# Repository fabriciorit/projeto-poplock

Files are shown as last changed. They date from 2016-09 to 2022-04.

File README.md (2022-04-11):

# Trava eletrônica controlada por padrão sonoro
Responsáveis: Caio Vinícius Batista Pereira e Fabrício Ribeiro Toloczko

## Introdução e Justificativa
A automatização residencial tem se tornado cada vez mais comum e mais barata. E uma das facilidades trazidas por este tipo de aplicação tecnológica é a dependência cada vez menor de falhas humanas. É comum as pessoas perderem ou esquecerem as chaves para entrar em casa, e muitas vezes as pessoas tem dificuldades para lembrar senhas. Músicas são trechos sonoros facilmente memorizáveis, além disso extremamente seguros, pois o número de músicas existentes é muito grande e disperso. 

## Especificação do Produto
* Reconhecimento de pelo menos 5 segundos de padrão sonoro;
* Resposta em frequência garantida para frequências médias(200Hz a 1500Hz);
* Tensão de alimentação 110/220V;
* Bateria de emergência;
* Gravação por microfone(eletreto);
* Acionamento de uma trava elétrica 12V de até 1A;
* Comunicação via módulo Wi-Fi usando TCP/IP;
* Interface com usuário via LED;
* Processamento de áudio em servidor alocado em um computador comum.

## Proposta técnica
A pessoa que deseja liberar a trava eletrônica emite um padrão sonoro. Este som é convertido por um sensor(microfone) que alimenta a entrada do microcontrolador. Este, converte o sinal analógico em sinal digital e envia-o pelo módulo de comunicação(Wi-Fi) para um computador, responsável por processar os dados de áudio recebidos.
O computador processará este áudio comparando-o  a um padrão de som de referência previamente configurado, que corresponde à senha de liberação da trava eletrônica. O computador retornará para o microcontrolador um comando de liberação, caso os sinais de áudio sejam considerados iguais, ou de falha de senha, caso os sinais sejam diferentes.
O microcontrolador, por sua vez, aguarda o recebimento de comandos do computador após enviar o som do microfone digitalizado. Ele executará cada comando dependendo de sua função. Duas funções básicas serão destravamento de porta e indicação de falha de senha — via interface com usuário por LED.
Haverá uma fonte de alimentação para os blocos do sistema projetado.

## Proposta de apresentação
Demonstrar o funcionamento do sistema. Este sistema será composto do dispositivo acondicionado em uma caixa plástica e a fechadura representada por uma trava elétrica automotiva — equivalente às de portas residenciais quanto ao princípio de funcionamento. O dispositivo estará ligado a um computador via interface Wi-Fi pela rede convencional.

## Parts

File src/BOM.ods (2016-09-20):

Reference |  | Value | Nota
SW1 | SPST | Buttons_Switches_ThroughHole:SW_PUSH-12mm
C2 | 10u | Capacitores:Cap_Eletrolitico_8x3.5
C3 | 10u | Capacitores:Cap_Eletrolitico_8x3.5
C6 | 10u | Capacitores:Cap_Eletrolitico_8x3.5
C1 | 220u16V | Capacitores:Cap_Eletrolitico_8x5
C4 | 100nF | Capacitores:Cap_MKT_EPCOS_7,3x2,5
C5 | 100nF | Capacitores:Cap_MKT_EPCOS_7,3x2,5
P3 | 12V Connector | Connect:BARREL_JACK
P4 | LOCK_CONNECTOR | Connect:Wafer_Vertical15x5.8x7RM2.5-5 | Par macho e fêmea, pinos
D1 | 1N4007 | Diodes_ThroughHole:Diode_DO-41_SOD81_Horizontal_RM10
D2 | 1N4007 | Diodes_ThroughHole:Diode_DO-41_SOD81_Horizontal_RM10
U4 | MIC_ELECTRET | Eletreto
IC1 | L293D | Housings_DIP:DIP-16_W7.62mm_LongPads
D3 | LED VERDE | LEDs:LED-5MM
D4 | LED VERMELHO | LEDs:LED-5MM
P10 | CONN_02X06 | Pin_Headers:Pin_Header_Straight_2x06 | BARRA DE PINOS 2x40 pinos(dupla) ou 1x80 pinos(simples)
P1 | CONN_02X08 | Pin_Headers:Pin_Header_Straight_2x08
P9 | CONN_02X08 | Pin_Headers:Pin_Header_Straight_2x08
P2 | CONN_02X10 | Pin_Headers:Pin_Header_Straight_2x10
R29 | 1R | Resistors_ThroughHole:Resistor_Horizontal_RM15mm | 2.5W
R30 | 1R | Resistors_ThroughHole:Resistor_Horizontal_RM15mm | 2.5W
R31 | 150 | Resistors_ThroughHole:Resistor_Horizontal_RM7mm
R32 | 220 | Resistors_ThroughHole:Resistor_Horizontal_RM7mm
R33 | 220 | Resistors_ThroughHole:Resistor_Horizontal_RM7mm
R34 | 10k | Resistors_ThroughHole:Resistor_Horizontal_RM7mm
R37 | 1k | Resistors_ThroughHole:Resistor_Horizontal_RM7mm
U2 | LD1117S50CTR | TO_SOT_Packages_SMD:SOT-223 | Verificar preço, talvez comprar na internet
U3 | LD1117S33CTR | TO_SOT_Packages_SMD:SOT-223 | Verificar preço, talvez comprar na internet
Q1 | 2n7000 | TO_SOT_Packages_THT:TO-92_Inline_Narrow_Oval
Q2 | 2n7000 | TO_SOT_Packages_THT:TO-92_Inline_Narrow_Oval
Q3 | 2n7000 | TO_SOT_Packages_THT:TO-92_Inline_Narrow_Oval

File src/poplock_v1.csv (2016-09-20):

Reference | Value | Footprint | Datasheet | MP | Price | MF | Description | Availability | Nota
P9 | CONN_02X08 | Pin_Headers:Pin_Header_Straight_2x08
P1 | CONN_02X08 | Pin_Headers:Pin_Header_Straight_2x08
P10 | CONN_02X06 | Pin_Headers:Pin_Header_Straight_2x06
P2 | CONN_02X10 | Pin_Headers:Pin_Header_Straight_2x10
U1 | ESP-12E | lib:ESP-12E
R4 | 0R | Resistors_SMD:R_0603_HandSoldering
R1 | 0R | Resistors_SMD:R_0603_HandSoldering
R5 | 0R | Resistors_SMD:R_0603_HandSoldering
R2 | 0R | Resistors_SMD:R_0603_HandSoldering
R6 | 0R | Resistors_SMD:R_0603_HandSoldering
R3 | 0R | Resistors_SMD:R_0603_HandSoldering
R7 | 0R | Resistors_SMD:R_0603_HandSoldering
R8 | 0R | Resistors_SMD:R_0603_HandSoldering
R18 | 0R | Resistors_SMD:R_0603_HandSoldering
R21 | 0R | Resistors_SMD:R_0603_HandSoldering
R17 | 0R | Resistors_SMD:R_0603_HandSoldering
R20 | 0R | Resistors_SMD:R_0603_HandSoldering
R16 | 0R | Resistors_SMD:R_0603_HandSoldering
R19 | 0R | Resistors_SMD:R_0603_HandSoldering
R15 | 0R | Resistors_SMD:R_0603_HandSoldering
R9 | 0R | Resistors_SMD:R_0603_HandSoldering
R12 | 0R | Resistors_SMD:R_0603_HandSoldering
R10 | 0R | Resistors_SMD:R_0603_HandSoldering
R13 | 0R | Resistors_SMD:R_0603_HandSoldering
R11 | 0R | Resistors_SMD:R_0603_HandSoldering
R14 | 0R | Resistors_SMD:R_0603_HandSoldering
R22 | 0R | Resistors_SMD:R_0603_HandSoldering
R26 | 0R | Resistors_SMD:R_0603_HandSoldering
R27 | 0R | Resistors_SMD:R_0603_HandSoldering
R28 | 0R | Resistors_SMD:R_0603_HandSoldering
R23 | 0R | Resistors_SMD:R_0603_HandSoldering
R24 | 0R | Resistors_SMD:R_0603_HandSoldering
R25 | 0R | Resistors_SMD:R_0603_HandSoldering
P3 | 12V Connector | Connect:BARREL_JACK
D2 | 1N4007 | Diodes_ThroughHole:Diode_DO-41_SOD81_Horizontal_RM10
U3 | LD1117S33CTR | TO_SOT_Packages_SMD:SOT-223
U2 | LD1117S50CTR | TO_SOT_Packages_SMD:SOT-223
C1 | 220u16V | Capacitores:Cap_Eletrolitico_8x5
C2 | 10u | Capacitores:Cap_Eletrolitico_8x3.5
C3 | 10u | Capacitores:Cap_Eletrolitico_8x3.5
D1 | 1N4007 | Diodes_ThroughHole:Diode_DO-41_SOD81_Horizontal_RM10
IC1 | L293D | Housings_DIP:DIP-16_W7.62mm_LongPads | DIP-16 STMicroelectronics | ,L293D,2.41 USD,STMicroelectronics,Driver; 36V; Power DIP; 600mA Low LevelO/P; 1.2A O/P High Level; 4 Drivers; 7V,Good,
P4 | LOCK_CONNECTOR | Connect:Wafer_Vertical15x5.8x7RM2.5-5
R29 | R | Resistors_ThroughHole:Resistor_Horizontal_RM15mm |  | ,,,,,,NOTA3
R30 | R | Resistors_ThroughHole:Resistor_Horizontal_RM15mm |  | ,,,,,,NOTA3
C5 | 100nF | Capacitores:Cap_MKT_EPCOS_7,3x2,5 |  | ,,,,,,NOTA2
C4 | 100nF | Capacitores:Cap_MKT_EPCOS_7,3x2,5 |  | ,,,,,,NOTA2
R36 | 0R | Resistors_SMD:R_1210_HandSoldering
R35 | 0R | Resistors_SMD:R_1210_HandSoldering
Q1 | 2n7000 | TO_SOT_Packages_THT:TO-92_Inline_Narrow_Oval
Q2 | 2n7000 | TO_SOT_Packages_THT:TO-92_Inline_Narrow_Oval
D3 | LED VERDE | LEDs:LED-5MM
D4 | LED VERMELHO | LEDs:LED-5MM
R31 | 150 | Resistors_ThroughHole:Resistor_Horizontal_RM7mm
R32 | 220 | Resistors_ThroughHole:Resistor_Horizontal_RM7mm
SW1 | SPST | Buttons_Switches_ThroughHole:SW_PUSH-12mm
R33 | 220 | Resistors_ThroughHole:Resistor_Horizontal_RM7mm
R34 | 10000 | Resistors_ThroughHole:Resistor_Horizontal_RM7mm
U4 | MIC_ELECTRET | Capacitors_ThroughHole:C_Radial_D10_L20_P2.5
Q3 | 2n7000 | TO_SOT_Packages_THT:TO-92_Inline_Narrow_Oval
C6 | 10u | Capacitores:Cap_Eletrolitico_8x3.5
R37 | 1k | Resistors_ThroughHole:Resistor_Horizontal_RM7mm

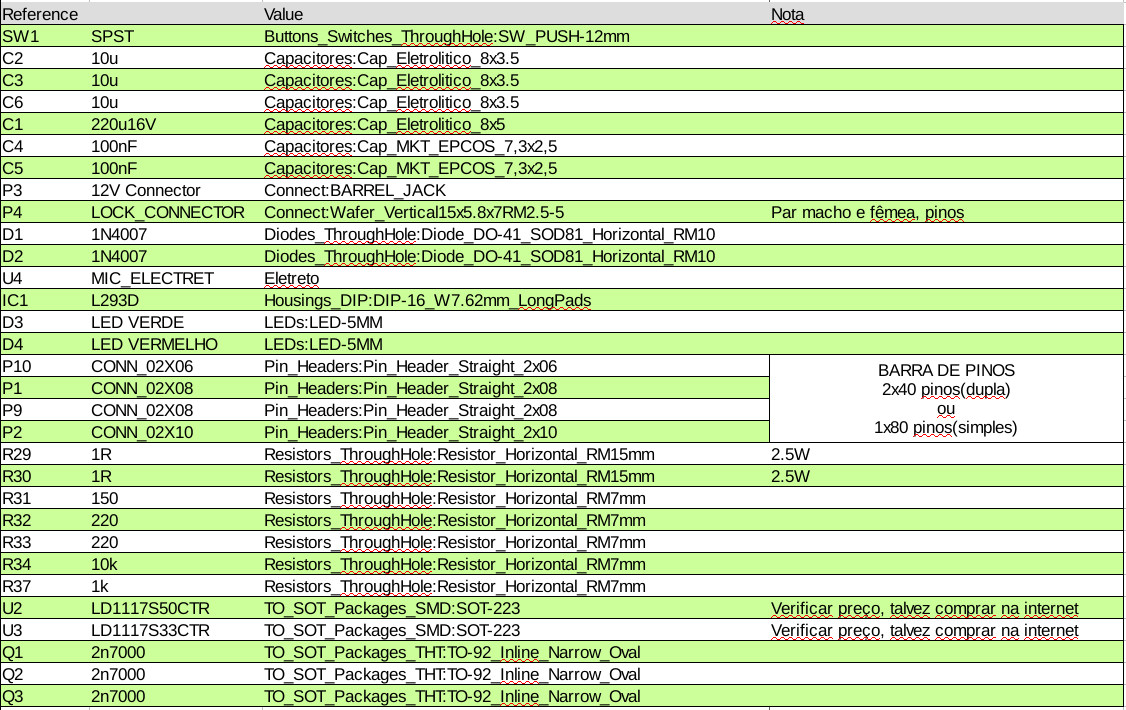
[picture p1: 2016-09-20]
src/BOM.png

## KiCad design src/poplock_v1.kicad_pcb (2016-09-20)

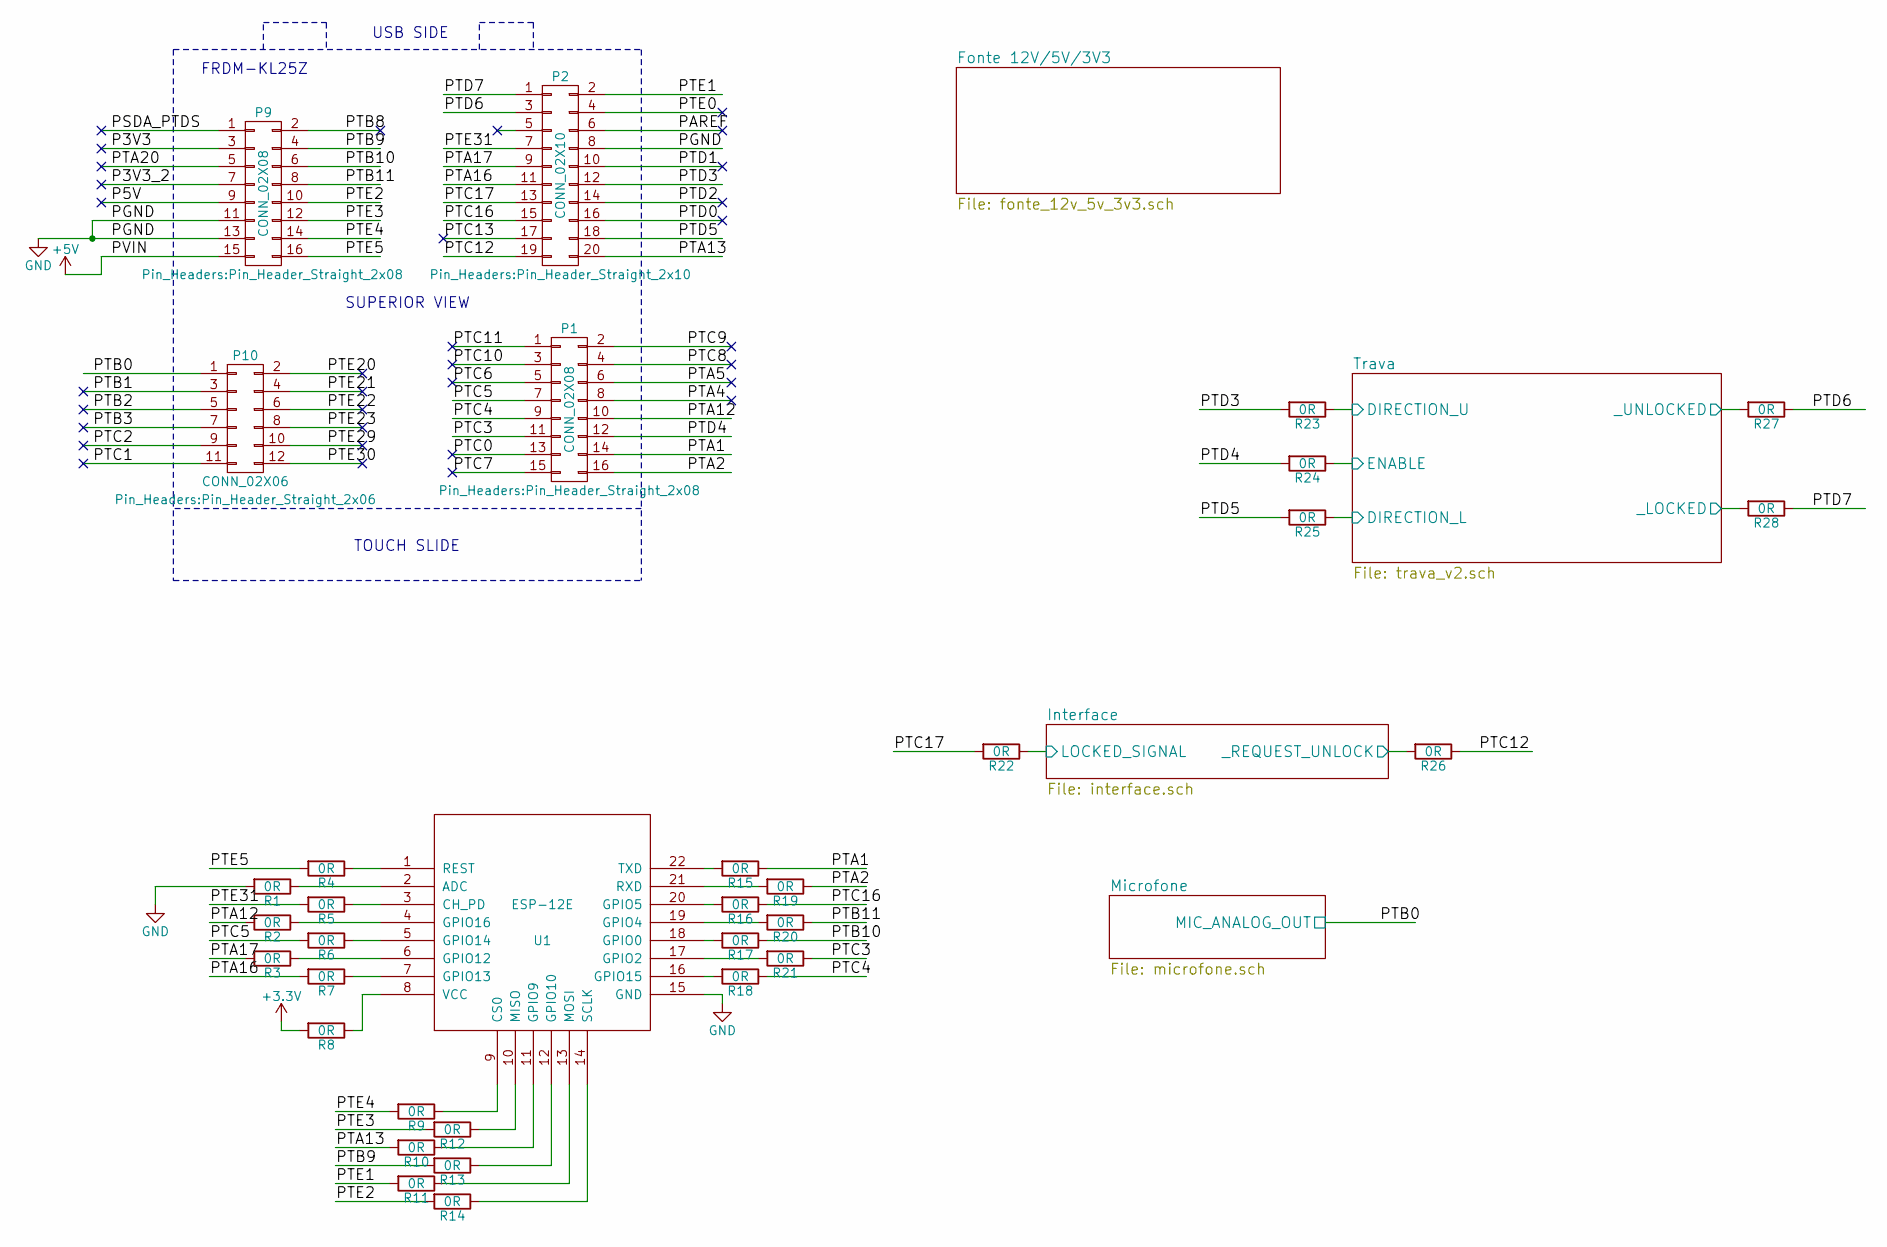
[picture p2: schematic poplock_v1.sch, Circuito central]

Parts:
P1, P9: CONN_02X08; Pin_Header_Straight_2x08
P2: CONN_02X10; Pin_Header_Straight_2x10
P10: CONN_02X06; Pin_Header_Straight_2x06
R1, R2, R3, R4, R5, R6, R7, R8, R9, R10, R11, R12, R13, R14, R15, R16, R17, R18, R19, R20, R21, R22, R23, R24, R25, R26, R27, R28: 0R; R_0603_HandSoldering
U1: ESP-12E

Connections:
+3V3: R8.2; also elsewhere on the board
+5V: P9.15; also elsewhere on the board
/Interface/LOCKED_SIGNAL: R22.1; also elsewhere on the board
/Interface/_REQUEST_UNLOCK: R26.2; also elsewhere on the board
/Microfone/MIC_ANALOG_OUT: P10.1; also elsewhere on the board
/P3V3: P9.3
/P3V3_2: P9.7
/P5V: P9.9
/PAREF: P2.6
/PSDA_PTDS: P9.1
/PTA1: P1.14, R15.1
/PTA2: P1.16, R19.1
/PTA4: P1.8
/PTA5: P1.6
/PTA12: P1.10, R2.2
/PTA13: P2.20, R10.2
/PTA16: P2.11, R7.2
/PTA17: P2.9, R3.2
/PTA20: P9.5
/PTB1: P10.3
/PTB2: P10.5
/PTB3: P10.7
/PTB8: P9.2
/PTB9: P9.4, R13.2
/PTB10: P9.6, R17.1
/PTB11: P9.8, R20.1
/PTC0: P1.13
/PTC1: P10.11
/PTC2: P10.9
/PTC3: P1.11, R21.1
/PTC4: P1.9, R18.1
/PTC5: P1.7, R6.2
/PTC6: P1.5
/PTC7: P1.15
/PTC8: P1.4
/PTC9: P1.2
/PTC10: P1.3
/PTC11: P1.1
/PTC12: P2.19, R26.1
/PTC13: P2.17
/PTC16: P2.15, R16.1
/PTC17: P2.13, R22.2
/PTD0: P2.16
/PTD1: P2.10
/PTD2: P2.14
/PTD3: P2.12, R23.2
/PTD4: P1.12, R24.2
/PTD5: P2.18, R25.2
/PTD6: P2.3, R27.1
/PTD7: P2.1, R28.1
/PTE0: P2.4
/PTE1: P2.2, R11.2
/PTE2: P9.10, R14.2
/PTE3: P9.12, R12.2
/PTE4: P9.14, R9.2
/PTE5: P9.16, R4.2
/PTE20: P10.2
/PTE21: P10.4
/PTE22: P10.6
/PTE23: P10.8
/PTE29: P10.10
/PTE30: P10.12
/PTE31: P2.7, R5.2
/Trava/DIRECTION_L: R25.1; also elsewhere on the board
/Trava/DIRECTION_U: R23.1; also elsewhere on the board
/Trava/ENABLE: R24.1; also elsewhere on the board
/Trava/_LOCKED: R28.2; also elsewhere on the board
/Trava/_UNLOCKED: R27.2; also elsewhere on the board
GND: P2.8, P9.11, P9.13, R1.2, U1.15 (GND); also elsewhere on the board
unnamed: R1.1, U1.2 (ADC)
unnamed: R2.1, U1.4 (GPIO16)
unnamed: R3.1, U1.6 (GPIO12)
unnamed: R4.1, U1.1 (REST)
unnamed: R5.1, U1.3 (CH_PD)
unnamed: R6.1, U1.5 (GPIO14)
unnamed: R7.1, U1.7 (GPIO13)
unnamed: R8.1, U1.8 (VCC)
unnamed: R9.1, U1.9 (CS0)
unnamed: R10.1, U1.11 (GPIO9)
unnamed: R11.1, U1.13 (MOSI)
unnamed: R12.1, U1.10 (MISO)
unnamed: R13.1, U1.12 (GPIO10)
unnamed: R14.1, U1.14 (SCLK)
unnamed: R15.2, U1.22 (TXD)
unnamed: R16.2, U1.20 (GPIO5)
unnamed: R17.2, U1.18 (GPIO0)
unnamed: R18.2, U1.16 (GPIO15)
unnamed: R19.2, U1.21 (RXD)
unnamed: R20.2, U1.19 (GPIO4)
unnamed: R21.2, U1.17 (GPIO2)

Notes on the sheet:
TOUCH SLIDE
SUPERIOR VIEW
USB SIDE
FRDM-KL25Z

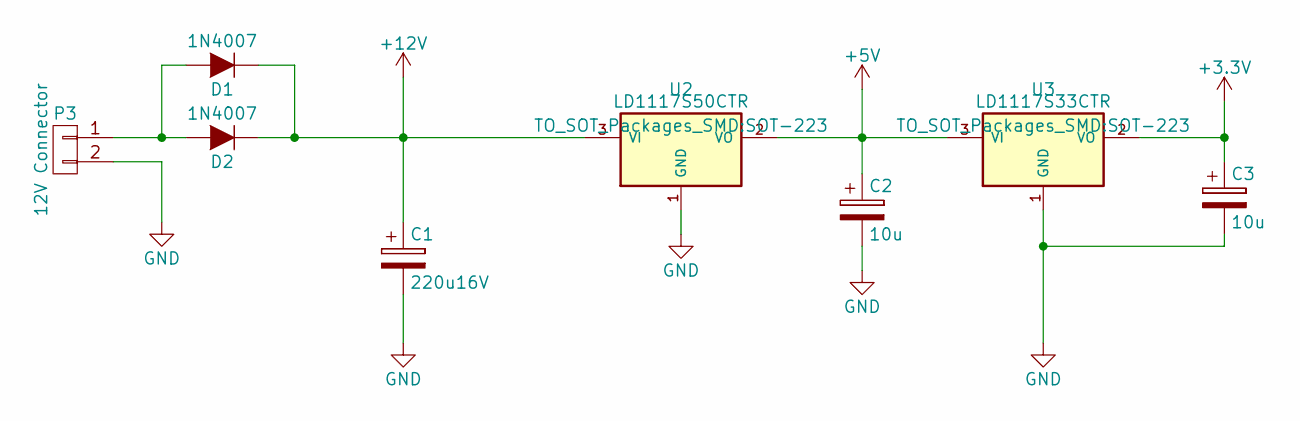
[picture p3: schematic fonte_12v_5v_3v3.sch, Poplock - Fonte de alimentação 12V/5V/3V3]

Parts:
C1: 220u16V; Cap_Eletrolitico_8x5
C2, C3: 10u; Cap_Eletrolitico_8x3.5
D1, D2: 1N4007; Diode_DO-41_SOD81_Horizontal_RM10
P3: 12V Connector; BARREL_JACK
U2: LD1117S50CTR; SOT-223
U3: LD1117S33CTR; SOT-223

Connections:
+3V3: C3.1, U3.2 (VO); also elsewhere on the board
+5V: C2.1, U2.2 (VO), U3.3 (VI); also elsewhere on the board
+12V: C1.1, D1.1 (K), D2.1 (K), U2.3 (VI); also elsewhere on the board
GND: C1.2, C2.2, C3.2, P3.2, U2.1 (GND), U3.1 (GND); also elsewhere on the board
unnamed: D1.2 (A), D2.2 (A), P3.1

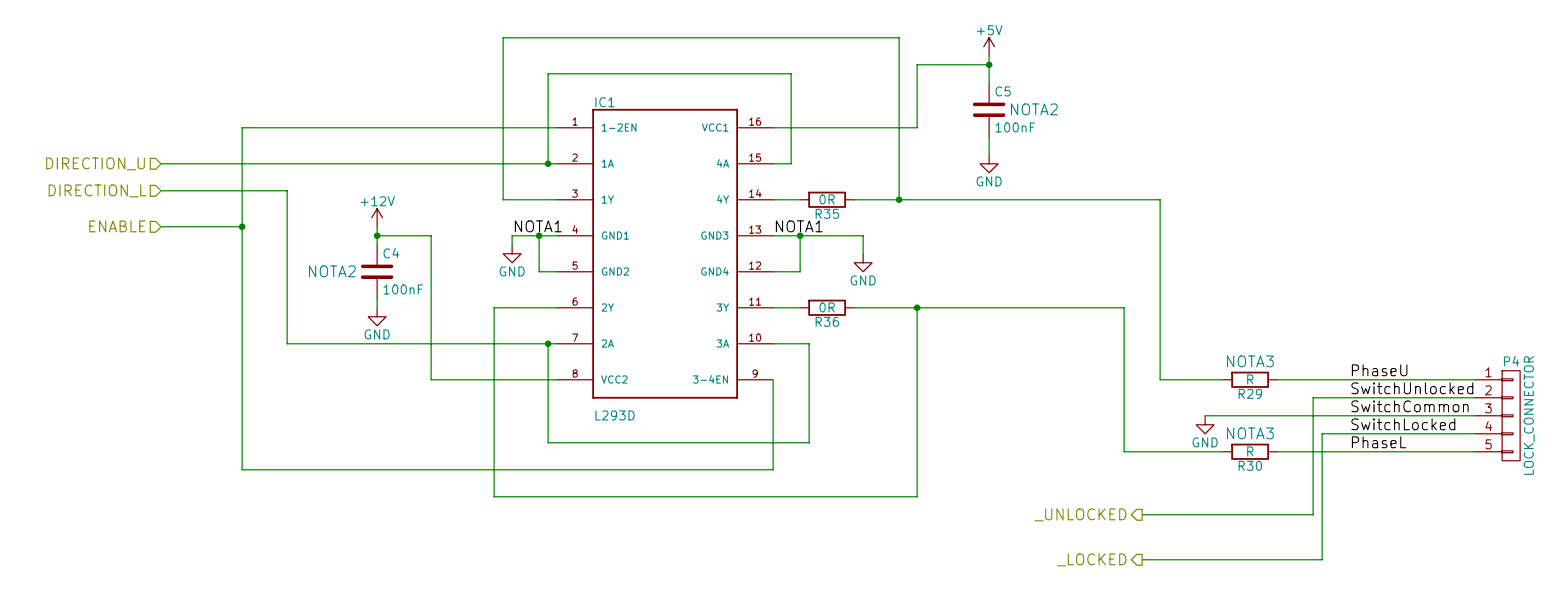
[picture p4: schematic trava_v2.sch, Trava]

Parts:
C4, C5: 100nF; Cap_MKT_EPCOS_7,3x2,5
IC1: L293D; DIP-16_W7.62mm_LongPads
P4: LOCK_CONNECTOR; Wafer_Vertical15x5.8x7RM2.5-5
R29, R30: R; Resistor_Horizontal_RM15mm
R35, R36: 0R; R_1210_HandSoldering

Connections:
+5V: C5.1, IC1.16 (VCC1); also elsewhere on the board
+12V: C4.1, IC1.8 (VCC2); also elsewhere on the board
/Trava/DIRECTION_L: IC1.7 (2A), IC1.10 (3A); also elsewhere on the board
/Trava/DIRECTION_U: IC1.2 (1A), IC1.15 (4A); also elsewhere on the board
/Trava/ENABLE: IC1.1 (1-2EN), IC1.9 (3-4EN); also elsewhere on the board
/Trava/PhaseL: P4.5, R30.1
/Trava/PhaseU: P4.1, R29.1
/Trava/_LOCKED: P4.4; also elsewhere on the board
/Trava/_UNLOCKED: P4.2; also elsewhere on the board
GND: C4.2, C5.2, IC1.4 (GND1), IC1.5 (GND2), IC1.12 (GND4), IC1.13 (GND3), P4.3; also elsewhere on the board
unnamed: IC1.3 (1Y), R29.2, R35.1
unnamed: IC1.6 (2Y), R30.2, R36.1
unnamed: IC1.11 (3Y), R36.2
unnamed: IC1.14 (4Y), R35.2

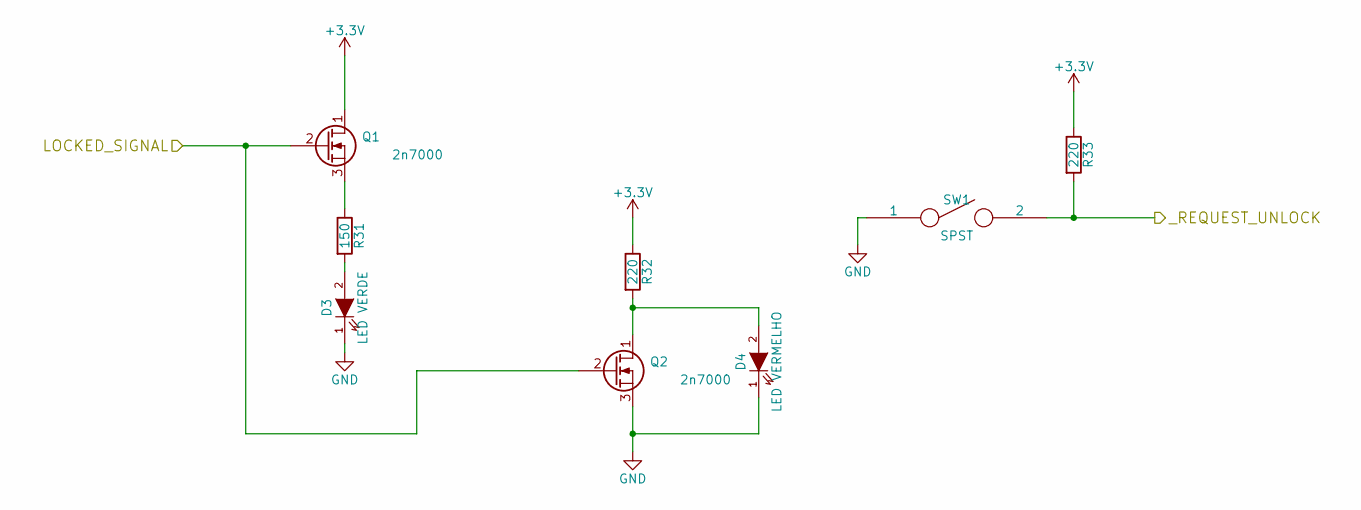
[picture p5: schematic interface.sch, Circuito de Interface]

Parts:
D3: LED VERDE; LED-5MM
D4: LED VERMELHO; LED-5MM
Q1, Q2: 2n7000; TO-92_Inline_Narrow_Oval
R31: 150; Resistor_Horizontal_RM7mm
R32, R33: 220; Resistor_Horizontal_RM7mm
SW1: SPST; SW_PUSH-12mm

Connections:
+3V3: Q1.1 (D), R32.1, R33.1; also elsewhere on the board
/Interface/LOCKED_SIGNAL: Q1.2 (G), Q2.2 (G); also elsewhere on the board
/Interface/_REQUEST_UNLOCK: R33.2, SW1.2; also elsewhere on the board
GND: D3.1 (K), D4.1 (K), Q2.3 (S), SW1.1; also elsewhere on the board
unnamed: D3.2 (A), R31.2
unnamed: D4.2 (A), Q2.1 (D), R32.2
unnamed: Q1.3 (S), R31.1

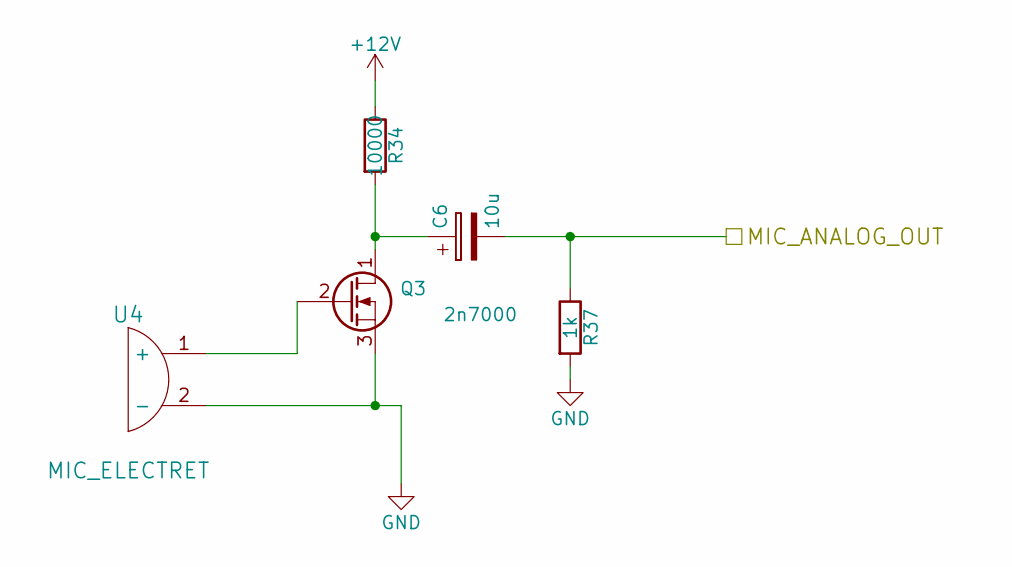
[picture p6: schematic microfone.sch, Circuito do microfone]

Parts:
C6: 10u; Cap_Eletrolitico_8x3.5
Q3: 2n7000; TO-92_Inline_Narrow_Oval
R34: 10000; Resistor_Horizontal_RM7mm
R37: 1k; Resistor_Horizontal_RM7mm
U4: MIC_ELECTRET; C_Radial_D10_L20_P2.5

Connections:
+12V: R34.1; also elsewhere on the board
/Microfone/MIC_ANALOG_OUT: C6.2, R37.1; also elsewhere on the board
GND: Q3.3 (S), R37.2, U4.2 (-); also elsewhere on the board
unnamed: C6.1, Q3.1 (D), R34.2
unnamed: Q3.2 (G), U4.1 (+)

Board: 2 copper layers, 62 parts (29 on the bottom side), 71 nets, no tracks yet.

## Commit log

2016-08-28 primeira versao do circuito da trava eletrica e da fonte de alimentacao
    [fonte.sch, poplock_v1.kicad_pcb, trava.sch]
2016-09-05 Modifiquei alguns arquivos e criei uma hierarquia no circuito.
    [fonte_12v_5v_3v3.sch, poplock_v1.sch, trava_v2.kicad_pcb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]
2016-09-05 cicuito mic sem hierarquia
    [fonte_12v_5v_3v3.sch, poplock_v1.sch, trava_v2.sch]
2016-09-05 Módulo de interface
    [fonte_12v_5v_3v3.sch, interface.sch, poplock_v1.sch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]
2016-09-05 Criada hierarquia para o circuito do microfone
    [fonte_12v_5v_3v3.sch, microfone.sch, poplock_v1.sch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]
2016-09-07 Adicionados conectores da FRDM-KL25Z e conexões básicas de alimentação
    [ESP12E.sch, fonte_12v_5v_3v3.sch, interface.sch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]
2016-09-07 Tabela de pinos ESP12E e FRDM-KL25Z
    [pin_table.ods]
2016-09-07 Atualização da tabela de pinos acrescentando os outros módulos(microfone e trava)
    [pin_table.ods]
2016-09-08 Acréscimo de bibliotecas de símbolo e de footprint do ESP12E retiradas de https://github.com/jdunmire/kicad-ESP8266 . As conexões necessárias com a KL25Z também foram realizadas.
    [ESP12E.sch, fonte_12v_5v_3v3.sch, interface.sch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]
2016-09-08 Substituição dos transitores NMOS pelo transistor 2n7000
    [interface.sch, microfone.sch]
2016-09-08 Verificação ERC -- checagem de erros elétricos no esquema -- concluída com sucesso. Há apenas dois warnings que não indicam problemas.
    [fonte_12v_5v_3v3.sch, interface.sch, microfone.sch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]
2016-09-09 Footprint atualizado
    [fonte_12v_5v_3v3.sch, interface.sch, microfone.sch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]
2016-09-09 Movida a pasta lib para dentro da pasta src. Preparado o arquivo de netlist e o da edição da PCB. A mudança de pastas permite referenciar os componentes usando variáveis de ambiente no KiCAD. Isso el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
    [poplock_v1.kicad_pcb]
2016-09-10 Definidas as dimensões necessárias(posição dos conectores, furos e bordas da FRDM-KL25Z) para criação do shield
    [poplock_v1.kicad_pcb]
2016-09-10 Corrigidas dimensões de comprimento da placa que estavam referenciadas num ponto errado.
    [poplock_v1.kicad_pcb]
2016-09-10 Distribuidos os componentes sobre a placa.
    [poplock_v1.kicad_pcb]
2016-09-20 Gerada a lista de materiais(BOM)
    [BOM.ods, poplock_v1.csv]
